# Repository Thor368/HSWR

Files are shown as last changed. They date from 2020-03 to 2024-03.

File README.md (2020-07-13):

# HSWR
Fork of the original VESC V6 to support up to 200V and 100A (depending on cooling)

#Work in progress (see http://vedder.se/forums/viewtopic.php?f=16&t=568)

#Gen1
Alpha Prototype on self etched boards. Never worked properly.

#Gen2
Four layer design in industry production quality. First working prototype.

#Gen3
Thicker copper layers for higher current capability. Had issues with current sampling.

#Gen3.1
Never was a board but a mod of Gen3. First prototype with Hall current sensors. Worked very well but needed a proper board.

#Gen4
- changed current sensors to halleffect sensors
- many changes in the IO (including connectors breaking backwards compatibility)
- HSWR can now interface with Tritium motor interface boards
- IO now fully isolated from HV
- fan drive
- changed MOSFET mounting mechanism for higher clamping force and reliablity
- some minimal mechanical changes breaking backwards compatibility to HSWR3 housing

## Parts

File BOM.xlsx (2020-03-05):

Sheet: Tabelle1
Reference(s) | Value | Footprint
C1, C12, C26, C29, C48, C49, C50, C51, C55, C56, C57, C58, C59 | 100n | Capacitor_SMD:C_0805_2012Metric
C2, C9 | 100u/16V | Capacitor_THT:CP_Radial_D6.3mm_P2.50mm
C3 | 22u/16V | Capacitor_SMD:C_0805_2012Metric
C4, C10, C11, C36 | 22u/6V3 | Capacitor_SMD:C_0805_2012Metric
C5, C6 | 2u2 | Capacitor_SMD:C_0805_2012Metric
C7, C8, C52, C53, C54 | 100n | Capacitor_SMD:C_0805_2012Metric
C13, C27, C30, C34, C35, C37, C38, C39, C40, C41, C42, C43, C44, C45, C46, C47 | 1u | Capacitor_SMD:C_0805_2012Metric
C14, C15, C17, C18, C19 | 330u 250V | Capacitor_THT:CP_Radial_D22.0mm_P10.00mm_SnapIn
C16, C28, C31 | 4n7 | Capacitor_SMD:C_0805_2012Metric
C20, C21, C22, C23, C24, C25 | 2u2 250V | Capacitor_SMD:C_2220_5650Metric
C32, C33 | 15p | Capacitor_SMD:C_0805_2012Metric
D1, D2, D3 | LED | LED_SMD:LED_0805_2012Metric
D10, D11, D12 | RFN2L4S | Diode_SMD:D_SOD-123
IC1 | B1212S-2W | Converter_DCDC:Converter_DCDC_muRata_NMAxxxxSC_THT
IC2, IC3 | JW5052C | Package_TO_SOT_SMD:TSOT-23-6
IC4 | ADUM3054 | Package_SO:SOIC-16W_7.5x10.3mm_P1.27mm
IC5 | ADuM4160 | Package_SO:SOIC-16W_7.5x10.3mm_P1.27mm
J1 | USB_B | Connector_USB:USB_B_TE_5787834_Vertical
J2 | IO | Connector_IDC:IDC-Header_2x08_P2.54mm_Vertical_Lock
J3 | B+ | MountingHole:MountingHole_6.5mm_Pad_Via
J4 | B- | MountingHole:MountingHole_6.5mm_Pad_Via
J5 | U | MountingHole:MountingHole_6.5mm_Pad_Via
J6 | V | MountingHole:MountingHole_6.5mm_Pad_Via
J7 | W | MountingHole:MountingHole_6.5mm_Pad_Via
J8 | SWD | Connector_PinHeader_2.54mm:PinHeader_2x03_P2.54mm_Vertical
J9 | AVR-ISP-6 | Connector_PinSocket_2.54mm:PinSocket_2x03_P2.54mm_Vertical
JP1 | H1 | Jumper:SolderJumper-2_P1.3mm_Open_TrianglePad1.0x1.5mm
JP2 | UART | Jumper:SolderJumper-3_P2.0mm_Open_TrianglePad1.0x1.5mm
JP3 | H2 | Jumper:SolderJumper-2_P1.3mm_Open_TrianglePad1.0x1.5mm
JP4 | H3 | Jumper:SolderJumper-2_P1.3mm_Open_TrianglePad1.0x1.5mm
L1, L2 | FCI201209F-4R7K | Inductor_SMD:L_0805_2012Metric
L3 | 22uH | Inductor_SMD:L_0805_2012Metric
NT1 | Net-Tie_2 | NetTie:NetTie-2_SMD_Pad2.0mm
Q1, Q2, Q3, Q4, Q5, Q6 | IXFK300N20X3 | Package_TO_SOT_THT:TO-264-3_Horizontal_TabUp
Q7 | Q_NMOS_GSD | Package_TO_SOT_SMD:SOT-23
R1, R37 | 100R | Resistor_SMD:R_0805_2012Metric
R2, R20, R23, R26, R36 | 1k | Resistor_SMD:R_0805_2012Metric
R3, R4, R33, R34, R40 | 120R | Resistor_SMD:R_0805_2012Metric
R5 | 470R | Resistor_SMD:R_0805_2012Metric
R6, R7 | 120R | Resistor_SMD:R_0805_2012Metric
R8, R27, R29, R31 | 300k 0.1% | Resistor_SMD:R_0805_2012Metric
R9, R28, R30, R32 | 4k7 0.1% | Resistor_SMD:R_0805_2012Metric
R10 | NTC | Resistor_SMD:R_0603_1608Metric
R11, R35 | 10k | Resistor_SMD:R_0805_2012Metric
R12, R13 | 100k | Resistor_SMD:R_0805_2012Metric
R14 | 110k | Resistor_SMD:R_0805_2012Metric
R15 | 15k | Resistor_SMD:R_0805_2012Metric
R16 | 49k9 | Resistor_SMD:R_0805_2012Metric
R17 | 11k | Resistor_SMD:R_0805_2012Metric
R18, R19, R21, R22, R24, R25 | 1R | Resistor_SMD:R_0805_2012Metric
R41, R42, R45, R46 | 22R | Resistor_SMD:R_0805_2012Metric
R43, R44 | 0R | Resistor_SMD:R_0805_2012Metric
U1, U2, U3 | ACS781xLRTR-150B | Sensor_Current:Allegro_PSOF-7_4.8x6.4mm_P1.60mm
U4 | STM32F405RGTx | Package_QFP:LQFP-64_10x10mm_P0.5mm
U5, U6, U7 | IRS2186 | Package_SO:SO-8_3.9x4.9mm_P1.27mm
U8 | AP1117-50 | Package_TO_SOT_SMD:SOT-223-3_TabPin2
U9 | ATtiny13A-SU | Package_SO:SOIJ-8_5.3x5.3mm_P1.27mm
U10 | AM26LV32xD | Package_SO:SOIC-16_3.9x9.9mm_P1.27mm
U11, U12 | ADuM120N | Package_SO:SOIC-8_3.9x4.9mm_P1.27mm
U13 | PC355 | Package_SO:SO-4_4.4x4.3mm_P2.54mm
Y1 | 8MHz | Crystal:Crystal_HC49-U_Vertical

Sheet: HSWR
Source:,"C:\Users\alexander.schroeder\git\HSWR\HSWR.sch"
Date:,"05.03.2020 09:08:09"
Tool:,"Eeschema (5.1.5)-3"
Generator:,"C:\Program Files\KiCad\bin\scripting\plugins/bom_csv_grouped_by_value.py"
Component Count:,"152"
Individual Components:
Item,"Qty","Reference(s)","Value","LibPart","Footprint","Datasheet"
,"","C1","100n","Device:C","Capacitor_SMD:C_0805_2012Metric",""
,"","C2","100u/16V","Device:CP_Small","Capacitor_THT:CP_Radial_D6.3mm_P2.50mm","~"
,"","C3","22u/16V","Device:C","Capacitor_SMD:C_0805_2012Metric","~"
,"","C4","22u/6V3","Device:C","Capacitor_SMD:C_0805_2012Metric","~"
,"","C5","2u2","Device:C_Small","Capacitor_SMD:C_0805_2012Metric","~"
,"","C6","2u2","Device:C_Small","Capacitor_SMD:C_0805_2012Metric","~"
,"","C7","100n","Device:C_Small","Capacitor_SMD:C_0805_2012Metric","~"
,"","C8","100n","Device:C_Small","Capacitor_SMD:C_0805_2012Metric","~"
,"","C9","100u/16V","Device:CP_Small","Capacitor_THT:CP_Radial_D6.3mm_P2.50mm","~"
,"","C10","22u/6V3","Device:C","Capacitor_SMD:C_0805_2012Metric","~"
,"","C11","22u/6V3","Device:C","Capacitor_SMD:C_0805_2012Metric","~"
,"","C12","100n","Device:C","Capacitor_SMD:C_0805_2012Metric","~"
,"","C13","1u","Device:C","Capacitor_SMD:C_0805_2012Metric","~"
,"","C14","330u 250V","Device:CP","Capacitor_THT:CP_Radial_D22.0mm_P10.00mm_SnapIn",""
,"","C15","330u 250V","Device:CP","Capacitor_THT:CP_Radial_D22.0mm_P10.00mm_SnapIn",""
,"","C16","4n7","Device:C","Capacitor_SMD:C_0805_2012Metric","~"
,"","C17","330u 250V","Device:CP","Capacitor_THT:CP_Radial_D22.0mm_P10.00mm_SnapIn",""
,"","C18","330u 250V","Device:CP","Capacitor_THT:CP_Radial_D22.0mm_P10.00mm_SnapIn",""
,"","C19","330u 250V","Device:CP","Capacitor_THT:CP_Radial_D22.0mm_P10.00mm_SnapIn",""
,"","C20","2u2 250V","Device:C","Capacitor_SMD:C_2220_5650Metric",""
,"","C21","2u2 250V","Device:C","Capacitor_SMD:C_2220_5650Metric",""
,"","C22","2u2 250V","Device:C","Capacitor_SMD:C_2220_5650Metric",""
,"","C23","2u2 250V","Device:C","Capacitor_SMD:C_2220_5650Metric",""
,"","C24","2u2 250V","Device:C","Capacitor_SMD:C_2220_5650Metric",""
,"","C25","2u2 250V","Device:C","Capacitor_SMD:C_2220_5650Metric",""
,"","C26","100n","Device:C","Capacitor_SMD:C_0805_2012Metric","~"
,"","C27","1u","Device:C","Capacitor_SMD:C_0805_2012Metric","~"
,"","C28","4n7","Device:C","Capacitor_SMD:C_0805_2012Metric","~"
,"","C29","100n","Device:C","Capacitor_SMD:C_0805_2012Metric","~"
,"","C30","1u","Device:C","Capacitor_SMD:C_0805_2012Metric","~"
,"","C31","4n7","Device:C","Capacitor_SMD:C_0805_2012Metric","~"
,"","C32","15p","Device:C","Capacitor_SMD:C_0805_2012Metric","~"
,"","C33","15p","Device:C","Capacitor_SMD:C_0805_2012Metric","~"
,"","C34","1u","Device:C","Capacitor_SMD:C_0805_2012Metric","~"
,"","C35","1u","Device:C","Capacitor_SMD:C_0805_2012Metric","~"
,"","C36","22u/6V3","Device:C","Capacitor_SMD:C_0805_2012Metric","~"
,"","C37","1u","Device:C","Capacitor_SMD:C_0805_2012Metric","~"
,"","C38","1u","Device:C","Capacitor_SMD:C_0805_2012Metric","~"
,"","C39","1u","Device:C","Capacitor_SMD:C_0805_2012Metric","~"
,"","C40","1u","Device:C","Capacitor_SMD:C_0805_2012Metric","~"
,"","C41","1u","Device:C","Capacitor_SMD:C_0805_2012Metric","~"
,"","C42","1u","Device:C","Capacitor_SMD:C_0805_2012Metric","~"
,"","C43","1u","Device:C","Capacitor_SMD:C_0805_2012Metric","~"
,"","C44","1u","Device:C","Capacitor_SMD:C_0805_2012Metric","~"
,"","C45","1u","Device:C","Capacitor_SMD:C_0805_2012Metric","~"
,"","C46","1u","Device:C","Capacitor_SMD:C_0805_2012Metric","~"
,"","C47","1u","Device:C","Capacitor_SMD:C_0805_2012Metric","~"
,"","C48","100n","Device:C","Capacitor_SMD:C_0805_2012Metric","~"
,"","C49","100n","Device:C","Capacitor_SMD:C_0805_2012Metric","~"
,"","C50","100n","Device:C","Capacitor_SMD:C_0805_2012Metric","~"
,"","C51","100n","Device:C","Capacitor_SMD:C_0805_2012Metric","~"
,"","C52","100n","Device:C_Small","Capacitor_SMD:C_0805_2012Metric",""
,"","C53","100n","Device:C_Small","Capacitor_SMD:C_0805_2012Metric",""
,"","C54","100n","Device:C_Small","Capacitor_SMD:C_0805_2012Metric",""
,"","C55","100n","Device:C","Capacitor_SMD:C_0805_2012Metric","~"
,"","C56","100n","Device:C","Capacitor_SMD:C_0805_2012Metric","~"
,"","C57","100n","Device:C","Capacitor_SMD:C_0805_2012Metric","~"
,"","C58","100n","Device:C","Capacitor_SMD:C_0805_2012Metric","~"
,"","C59","100n","Device:C","Capacitor_SMD:C_0805_2012Metric","~"
,"","D1","LED","Device:LED","LED_SMD:LED_0805_2012Metric","~"
,"","D2","LED","Device:LED","LED_SMD:LED_0805_2012Metric","~"
,"","D3","LED","Device:LED","LED_SMD:LED_0805_2012Metric","~"
,"","D10","RFN2L4S","Device:D_Small","Diode_SMD:D_SOD-123",""
,"","D11","RFN2L4S","Device:D_Small","Diode_SMD:D_SOD-123",""
,"","D12","RFN2L4S","Device:D_Small","Diode_SMD:D_SOD-123",""
,"","IC1","B1212S-2W","HSWR:DCDC_6pin","Converter_DCDC:Converter_DCDC_muRata_NMAxxxxSC_THT",""
,"","IC2","JW5052C","HSWR:JW5052C","Package_TO_SOT_SMD:TSOT-23-6",""
,"","IC3","JW5052C","HSWR:JW5052C","Package_TO_SOT_SMD:TSOT-23-6",""
,"","IC4","ADUM3054","HSWR:ADUM3054","Package_SO:SOIC-16W_7.5x10.3mm_P1.27mm",""
,"","IC5","ADuM4160","Interface_USB:ADUM4160","Package_SO:SOIC-16W_7.5x10.3mm_P1.27mm",""
,"","J1","USB_B","Connector:USB_B","Connector_USB:USB_B_TE_5787834_Vertical"," ~"
,"","J2","IO","Connector:Conn_01x16_Male","Connector_IDC:IDC-Header_2x08_P2.54mm_Vertical_Lock","~"
,"","J3","B+","Connector:Conn_01x01_Male","MountingHole:MountingHole_6.5mm_Pad_Via","~"
,"","J4","B-","Connector:Conn_01x01_Male","MountingHole:MountingHole_6.5mm_Pad_Via","~"
,"","J5","U","Connector:Conn_01x01_Male","MountingHole:MountingHole_6.5mm_Pad_Via","~"
,"","J6","V","Connector:Conn_01x01_Male","MountingHole:MountingHole_6.5mm_Pad_Via","~"
,"","J7","W","Connector:Conn_01x01_Male","MountingHole:MountingHole_6.5mm_Pad_Via","~"
,"","J8","SWD","Connector:Conn_01x06_Male","Connector_PinHeader_2.54mm:PinHeader_2x03_P2.54mm_Vertical","~"
,"","J9","AVR-ISP-6","Connector:AVR-ISP-6","Connector_PinSocket_2.54mm:PinSocket_2x03_P2.54mm_Vertical"," ~"
,"","JP1","H1","Device:Jumper_NO_Small","Jumper:SolderJumper-2_P1.3mm_Open_TrianglePad1.0x1.5mm","~"
,"","JP2","UART","Jumper:SolderJumper_3_Open","Jumper:SolderJumper-3_P2.0mm_Open_TrianglePad1.0x1.5mm","~"
,"","JP3","H2","Device:Jumper_NO_Small","Jumper:SolderJumper-2_P1.3mm_Open_TrianglePad1.0x1.5mm","~"
,"","JP4","H3","Device:Jumper_NO_Small","Jumper:SolderJumper-2_P1.3mm_Open_TrianglePad1.0x1.5mm","~"
,"","L1","FCI201209F-4R7K","Device:L","Inductor_SMD:L_0805_2012Metric","~"
,"","L2","FCI201209F-4R7K","Device:L","Inductor_SMD:L_0805_2012Metric","~"
,"","L3","22uH","Device:L","Inductor_SMD:L_0805_2012Metric","~"
,"","NT1","Net-Tie_2","Device:Net-Tie_2","NetTie:NetTie-2_SMD_Pad2.0mm","~"
,"","Q1","IXFK300N20X3","Device:Q_NMOS_GDS","Package_TO_SOT_THT:TO-264-3_Horizontal_TabUp",""
,"","Q2","IXFK300N20X3","Device:Q_NMOS_GDS","Package_TO_SOT_THT:TO-264-3_Horizontal_TabUp",""
,"","Q3","IXFK300N20X3","Device:Q_NMOS_GDS","Package_TO_SOT_THT:TO-264-3_Horizontal_TabUp",""
,"","Q4","IXFK300N20X3","Device:Q_NMOS_GDS","Package_TO_SOT_THT:TO-264-3_Horizontal_TabUp",""
,"","Q5","IXFK300N20X3","Device:Q_NMOS_GDS","Package_TO_SOT_THT:TO-264-3_Horizontal_TabUp",""
,"","Q6","IXFK300N20X3","Device:Q_NMOS_GDS","Package_TO_SOT_THT:TO-264-3_Horizontal_TabUp",""
,"","Q7","Q_NMOS_GSD","Device:Q_NMOS_GSD","Package_TO_SOT_SMD:SOT-23","~"
,"","R1","100R","Device:R","Resistor_SMD:R_0805_2012Metric","~"
,"","R2","1k","Device:R","Resistor_SMD:R_0805_2012Metric","~"
,"","R3","120R","Device:R_Small","Resistor_SMD:R_0805_2012Metric","~"
,"","R4","120R","Device:R_Small","Resistor_SMD:R_0805_2012Metric","~"
,"","R5","470R","Device:R","Resistor_SMD:R_0805_2012Metric","~"
,"","R6","120R","Device:R","Resistor_SMD:R_0805_2012Metric","~"
,"","R7","120R","Device:R","Resistor_SMD:R_0805_2012Metric","~"
,"","R8","300k 0.1%","Device:R","Resistor_SMD:R_0805_2012Metric",""
,"","R9","4k7 0.1%","Device:R","Resistor_SMD:R_0805_2012Metric",""
,"","R10","NTC","Device:Thermistor_NTC","Resistor_SMD:R_0603_1608Metric","~"
,"","R11","10k","Device:R","Resistor_SMD:R_0805_2012Metric","~"
,"","R12","100k","Device:R_Small","Resistor_SMD:R_0805_2012Metric","~"
,"","R13","100k","Device:R_Small","Resistor_SMD:R_0805_2012Metric","~"
,"","R14","110k","Device:R_Small","Resistor_SMD:R_0805_2012Metric","~"
,"","R15","15k","Device:R_Small","Resistor_SMD:R_0805_2012Metric","~"
,"","R16","49k9","Device:R_Small","Resistor_SMD:R_0805_2012Metric","~"
,"","R17","11k","Device:R_Small","Resistor_SMD:R_0805_2012Metric","~"
,"","R18","1R","Device:R","Resistor_SMD:R_0805_2012Metric",""
,"","R19","1R","Device:R","Resistor_SMD:R_0805_2012Metric",""
,"","R20","1k","Device:R","Resistor_SMD:R_0805_2012Metric","~"
,"","R21","1R","Device:R","Resistor_SMD:R_0805_2012Metric",""
,"","R22","1R","Device:R","Resistor_SMD:R_0805_2012Metric",""
,"","R23","1k","Device:R","Resistor_SMD:R_0805_2012Metric","~"
,"","R24","1R","Device:R","Resistor_SMD:R_0805_2012Metric",""
,"","R25","1R","Device:R","Resistor_SMD:R_0805_2012Metric",""
,"","R26","1k","Device:R","Resistor_SMD:R_0805_2012Metric","~"
,"","R27","300k 0.1%","Device:R","Resistor_SMD:R_0805_2012Metric","~"
,"","R28","4k7 0.1%","Device:R","Resistor_SMD:R_0805_2012Metric","~"
,"","R29","300k 0.1%","Device:R","Resistor_SMD:R_0805_2012Metric","~"
,"","R30","4k7 0.1%","Device:R","Resistor_SMD:R_0805_2012Metric","~"
,"","R31","300k 0.1%","Device:R","Resistor_SMD:R_0805_2012Metric","~"
,"","R32","4k7 0.1%","Device:R","Resistor_SMD:R_0805_2012Metric","~"
,"","R33","120R","Device:R_Small","Resistor_SMD:R_0805_2012Metric","~"
,"","R34","120R","Device:R_Small","Resistor_SMD:R_0805_2012Metric","~"
,"","R35","10k","Device:R","Resistor_SMD:R_0805_2012Metric","~"
,"","R36","1k","Device:R","Resistor_SMD:R_0805_2012Metric","~"
,"","R37","100R","Device:R","Resistor_SMD:R_0805_2012Metric","~"
,"","R40","120R","Device:R_Small","Resistor_SMD:R_0805_2012Metric",""
,"","R41","22R","Device:R","Resistor_SMD:R_0805_2012Metric","~"
,"","R42","22R","Device:R","Resistor_SMD:R_0805_2012Metric","~"
,"","R43","0R","Device:R","Resistor_SMD:R_0805_2012Metric","~"
,"","R44","0R","Device:R","Resistor_SMD:R_0805_2012Metric","~"
,"","R45","22R","Device:R","Resistor_SMD:R_0805_2012Metric","~"
,"","R46","22R","Device:R","Resistor_SMD:R_0805_2012Metric","~"
,"","U1","ACS781xLRTR-150B","Sensor_Current:ACS781xLRTR-150B","Sensor_Current:Allegro_PSOF-7_4.8x6.4mm_P1.60mm","http://www.allegromicro.com/~/media/Files/Datasheets/ACS781-Datsaheet.ashx?la=en"
,"","U2","ACS781xLRTR-150B","Sensor_Current:ACS781xLRTR-150B","Sensor_Current:Allegro_PSOF-7_4.8x6.4mm_P1.60mm","http://www.allegromicro.com/~/media/Files/Datasheets/ACS781-Datsaheet.ashx?la=en"
,"","U3","ACS781xLRTR-150B","Sensor_Current:ACS781xLRTR-150B","Sensor_Current:Allegro_PSOF-7_4.8x6.4mm_P1.60mm","http://www.allegromicro.com/~/media/Files/Datasheets/ACS781-Datsaheet.ashx?la=en"
,"","U4","STM32F405RGTx","MCU_ST_STM32F4:STM32F405RGTx","Package_QFP:LQFP-64_10x10mm_P0.5mm","http://www.st.com/st-web-ui/static/active/en/resource/technical/document/datasheet/DM00037051.pdf"
,"","U5","IRS2186","Driver_FET:IRS2186","Package_SO:SO-8_3.9x4.9mm_P1.27mm","http://www.irf.com/product-info/datasheets/data/irs2186pbf.pdf"
,"","U6","IRS2186","Driver_FET:IRS2186","Package_SO:SO-8_3.9x4.9mm_P1.27mm","http://www.irf.com/product-info/datasheets/data/irs2186pbf.pdf"
,"","U7","IRS2186","Driver_FET:IRS2186","Package_SO:SO-8_3.9x4.9mm_P1.27mm","http://www.irf.com/product-info/datasheets/data/irs2186pbf.pdf"
,"","U8","AP1117-50","HSWR:AP1117-50","Package_TO_SOT_SMD:SOT-223-3_TabPin2","http://www.diodes.com/datasheets/AP1117.pdf"
,"","U9","ATtiny13A-SU","MCU_Microchip_ATtiny:ATtiny13A-SU","Package_SO:SOIJ-8_5.3x5.3mm_P1.27mm","http://ww1.microchip.com/downloads/en/DeviceDoc/doc8126.pdf"
,"","U10","AM26LV32xD","Interface:AM26LV32xD","Package_SO:SOIC-16_3.9x9.9mm_P1.27mm","http://www.ti.com/lit/ds/symlink/am26lv32.pdf"
,"","U11","ADuM120N","Isolator:ADuM120N","Package_SO:SOIC-8_3.9x4.9mm_P1.27mm","https://www.analog.com/media/en/technical-documentation/data-sheets/ADuM120N_121N.pdf"
,"","U12","ADuM120N","Isolator:ADuM120N","Package_SO:SOIC-8_3.9x4.9mm_P1.27mm","https://www.analog.com/media/en/technical-documentation/data-sheets/ADuM120N_121N.pdf"
,"","U13","PC355","Isolator:SFH617A-1","Package_SO:SO-4_4.4x4.3mm_P2.54mm","http://www.vishay.com/docs/83740/sfh617a.pdf"
,"","Y1","8MHz","Device:Crystal","Crystal:Crystal_HC49-U_Vertical","~"
Collated Components:
Item,"Qty","Reference(s)","Value","LibPart","Footprint","Datasheet"
1,"13","C1, C12, C26, C29, C48, C49, C50, C51, C55, C56, C57, C58, C59","100n","Device:C","Capacitor_SMD:C_0805_2012Metric","~"
2,"2","C2, C9","100u/16V","Device:CP_Small","Capacitor_THT:CP_Radial_D6.3mm_P2.50mm","~"
3,"1","C3","22u/16V","Device:C","Capacitor_SMD:C_0805_2012Metric","~"
4,"4","C4, C10, C11, C36","22u/6V3","Device:C","Capacitor_SMD:C_0805_2012Metric","~"
5,"2","C5, C6","2u2","Device:C_Small","Capacitor_SMD:C_0805_2012Metric","~"
6,"5","C7, C8, C52, C53, C54","100n","Device:C_Small","Capacitor_SMD:C_0805_2012Metric","~"
7,"16","C13, C27, C30, C34, C35, C37, C38, C39, C40, C41, C42, C43, C44, C45, C46, C47","1u","Device:C","Capacitor_SMD:C_0805_2012Metric","~"
8,"5","C14, C15, C17, C18, C19","330u 250V","Device:CP","Capacitor_THT:CP_Radial_D22.0mm_P10.00mm_SnapIn",""
9,"3","C16, C28, C31","4n7","Device:C","Capacitor_SMD:C_0805_2012Metric","~"
10,"6","C20, C21, C22, C23, C24, C25","2u2 250V","Device:C","Capacitor_SMD:C_2220_5650Metric",""
11,"2","C32, C33","15p","Device:C","Capacitor_SMD:C_0805_2012Metric","~"
12,"3","D1, D2, D3","LED","Device:LED","LED_SMD:LED_0805_2012Metric","~"
13,"3","D10, D11, D12","RFN2L4S","Device:D_Small","Diode_SMD:D_SOD-123",""
14,"1","IC1","B1212S-2W","HSWR:DCDC_6pin","Converter_DCDC:Converter_DCDC_muRata_NMAxxxxSC_THT",""
15,"2","IC2, IC3","JW5052C","HSWR:JW5052C","Package_TO_SOT_SMD:TSOT-23-6",""
16,"1","IC4","ADUM3054","HSWR:ADUM3054","Package_SO:SOIC-16W_7.5x10.3mm_P1.27mm",""
17,"1","IC5","ADuM4160","Interface_USB:ADUM4160","Package_SO:SOIC-16W_7.5x10.3mm_P1.27mm",""
18,"1","J1","USB_B","Connector:USB_B","Connector_USB:USB_B_TE_5787834_Vertical"," ~"
19,"1","J2","IO","Connector:Conn_01x16_Male","Connector_IDC:IDC-Header_2x08_P2.54mm_Vertical_Lock","~"
20,"1","J3","B+","Connector:Conn_01x01_Male","MountingHole:MountingHole_6.5mm_Pad_Via","~"
21,"1","J4","B-","Connector:Conn_01x01_Male","MountingHole:MountingHole_6.5mm_Pad_Via","~"
22,"1","J5","U","Connector:Conn_01x01_Male","MountingHole:MountingHole_6.5mm_Pad_Via","~"
23,"1","J6","V","Connector:Conn_01x01_Male","MountingHole:MountingHole_6.5mm_Pad_Via","~"
24,"1","J7","W","Connector:Conn_01x01_Male","MountingHole:MountingHole_6.5mm_Pad_Via","~"
25,"1","J8","SWD","Connector:Conn_01x06_Male","Connector_PinHeader_2.54mm:PinHeader_2x03_P2.54mm_Vertical","~"
26,"1","J9","AVR-ISP-6","Connector:AVR-ISP-6","Connector_PinSocket_2.54mm:PinSocket_2x03_P2.54mm_Vertical"," ~"
27,"1","JP1","H1","Device:Jumper_NO_Small","Jumper:SolderJumper-2_P1.3mm_Open_TrianglePad1.0x1.5mm","~"
28,"1","JP2","UART","Jumper:SolderJumper_3_Open","Jumper:SolderJumper-3_P2.0mm_Open_TrianglePad1.0x1.5mm","~"
29,"1","JP3","H2","Device:Jumper_NO_Small","Jumper:SolderJumper-2_P1.3mm_Open_TrianglePad1.0x1.5mm","~"
30,"1","JP4","H3","Device:Jumper_NO_Small","Jumper:SolderJumper-2_P1.3mm_Open_TrianglePad1.0x1.5mm","~"
31,"2","L1, L2","FCI201209F-4R7K","Device:L","Inductor_SMD:L_0805_2012Metric","~"
32,"1","L3","22uH","Device:L","Inductor_SMD:L_0805_2012Metric","~"
33,"1","NT1","Net-Tie_2","Device:Net-Tie_2","NetTie:NetTie-2_SMD_Pad2.0mm","~"
34,"6","Q1, Q2, Q3, Q4, Q5, Q6","IXFK300N20X3","Device:Q_NMOS_GDS","Package_TO_SOT_THT:TO-264-3_Horizontal_TabUp",""
35,"1","Q7","Q_NMOS_GSD","Device:Q_NMOS_GSD","Package_TO_SOT_SMD:SOT-23","~"
36,"2","R1, R37","100R","Device:R","Resistor_SMD:R_0805_2012Metric","~"
37,"5","R2, R20, R23, R26, R36","1k","Device:R","Resistor_SMD:R_0805_2012Metric","~"
38,"5","R3, R4, R33, R34, R40","120R","Device:R_Small","Resistor_SMD:R_0805_2012Metric","~"
39,"1","R5","470R","Device:R","Resistor_SMD:R_0805_2012Metric","~"
40,"2","R6, R7","120R","Device:R","Resistor_SMD:R_0805_2012Metric","~"
41,"4","R8, R27, R29, R31","300k 0.1%","Device:R","Resistor_SMD:R_0805_2012Metric","~"
42,"4","R9, R28, R30, R32","4k7 0.1%","Device:R","Resistor_SMD:R_0805_2012Metric","~"
43,"1","R10","NTC","Device:Thermistor_NTC","Resistor_SMD:R_0603_1608Metric","~"
44,"2","R11, R35","10k","Device:R","Resistor_SMD:R_0805_2012Metric","~"
45,"2","R12, R13","100k","Device:R_Small","Resistor_SMD:R_0805_2012Metric","~"
46,"1","R14","110k","Device:R_Small","Resistor_SMD:R_0805_2012Metric","~"
47,"1","R15","15k","Device:R_Small","Resistor_SMD:R_0805_2012Metric","~"
48,"1","R16","49k9","Device:R_Small","Resistor_SMD:R_0805_2012Metric","~"
49,"1","R17","11k","Device:R_Small","Resistor_SMD:R_0805_2012Metric","~"
50,"6","R18, R19, R21, R22, R24, R25","1R","Device:R","Resistor_SMD:R_0805_2012Metric",""
51,"4","R41, R42, R45, R46","22R","Device:R","Resistor_SMD:R_0805_2012Metric","~"
52,"2","R43, R44","0R","Device:R","Resistor_SMD:R_0805_2012Metric","~"
53,"3","U1, U2, U3","ACS781xLRTR-150B","Sensor_Current:ACS781xLRTR-150B","Sensor_Current:Allegro_PSOF-7_4.8x6.4mm_P1.60mm","http://www.allegromicro.com/~/media/Files/Datasheets/ACS781-Datsaheet.ashx?la=en"
54,"1","U4","STM32F405RGTx","MCU_ST_STM32F4:STM32F405RGTx","Package_QFP:LQFP-64_10x10mm_P0.5mm","http://www.st.com/st-web-ui/static/active/en/resource/technical/document/datasheet/DM00037051.pdf"
55,"3","U5, U6, U7","IRS2186","Driver_FET:IRS2186","Package_SO:SO-8_3.9x4.9mm_P1.27mm","http://www.irf.com/product-info/datasheets/data/irs2186pbf.pdf"
56,"1","U8","AP1117-50","HSWR:AP1117-50","Package_TO_SOT_SMD:SOT-223-3_TabPin2","http://www.diodes.com/datasheets/AP1117.pdf"
57,"1","U9","ATtiny13A-SU","MCU_Microchip_ATtiny:ATtiny13A-SU","Package_SO:SOIJ-8_5.3x5.3mm_P1.27mm","http://ww1.microchip.com/downloads/en/DeviceDoc/doc8126.pdf"
58,"1","U10","AM26LV32xD","Interface:AM26LV32xD","Package_SO:SOIC-16_3.9x9.9mm_P1.27mm","http://www.ti.com/lit/ds/symlink/am26lv32.pdf"
59,"2","U11, U12","ADuM120N","Isolator:ADuM120N","Package_SO:SOIC-8_3.9x4.9mm_P1.27mm","https://www.analog.com/media/en/technical-documentation/data-sheets/ADuM120N_121N.pdf"
60,"1","U13","PC355","Isolator:SFH617A-1","Package_SO:SO-4_4.4x4.3mm_P2.54mm","http://www.vishay.com/docs/83740/sfh617a.pdf"
61,"1","Y1","8MHz","Device:Crystal","Crystal:Crystal_HC49-U_Vertical","~"

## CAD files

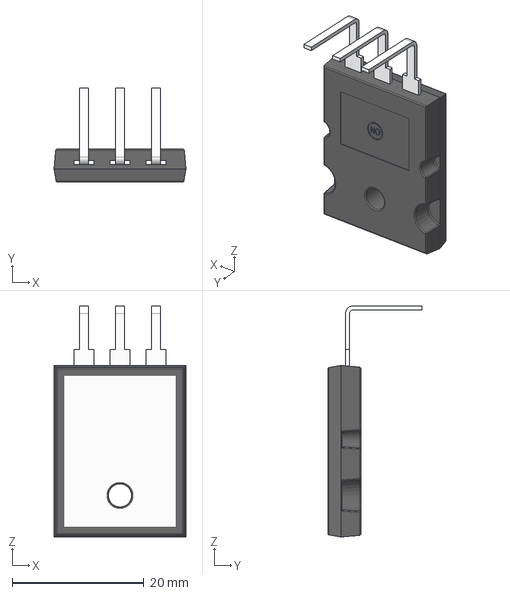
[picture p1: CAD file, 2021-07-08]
TO-264-3-HM.step
20.0 x 14.3 x 35.0 mm

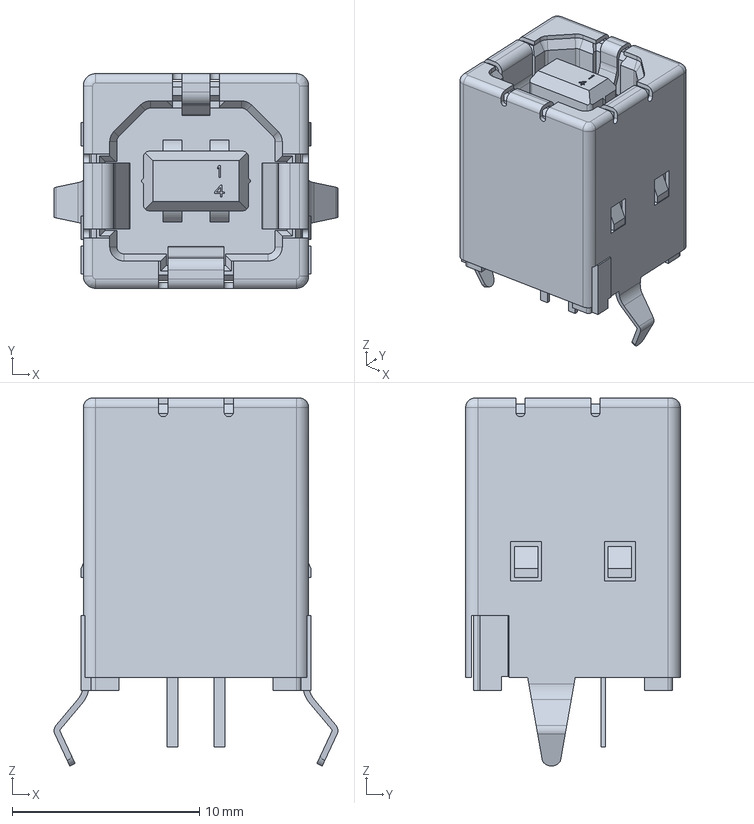
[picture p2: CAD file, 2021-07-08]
USB B vert.step
15.1 x 11.5 x 19.6 mm

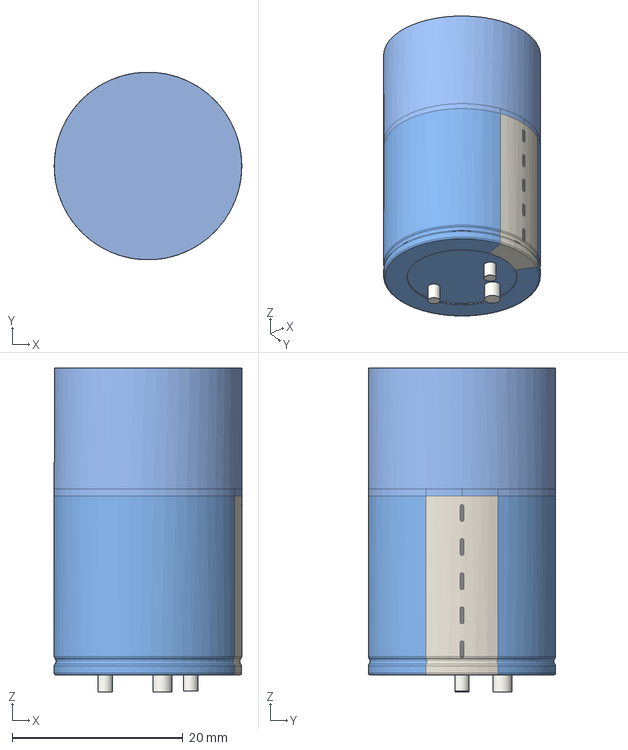
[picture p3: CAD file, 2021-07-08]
CP_Radial_D220mm_P1000mm_3pin_SnapIn.step
22.0 x 22.0 x 38.0 mm

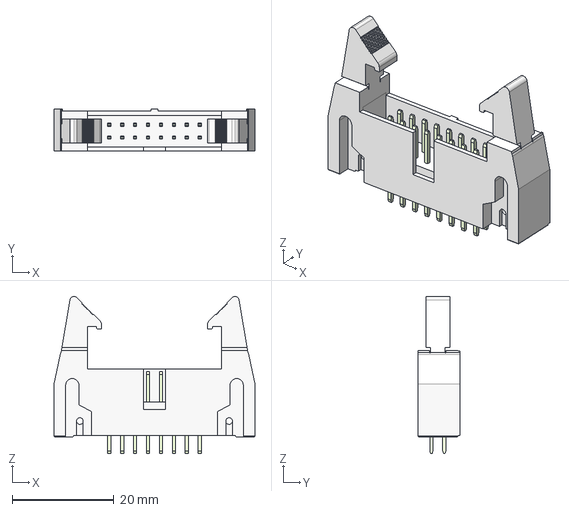
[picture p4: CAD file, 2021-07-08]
header_awh16g-0232-t.step
39.5 x 8.30 x 30.9 mm

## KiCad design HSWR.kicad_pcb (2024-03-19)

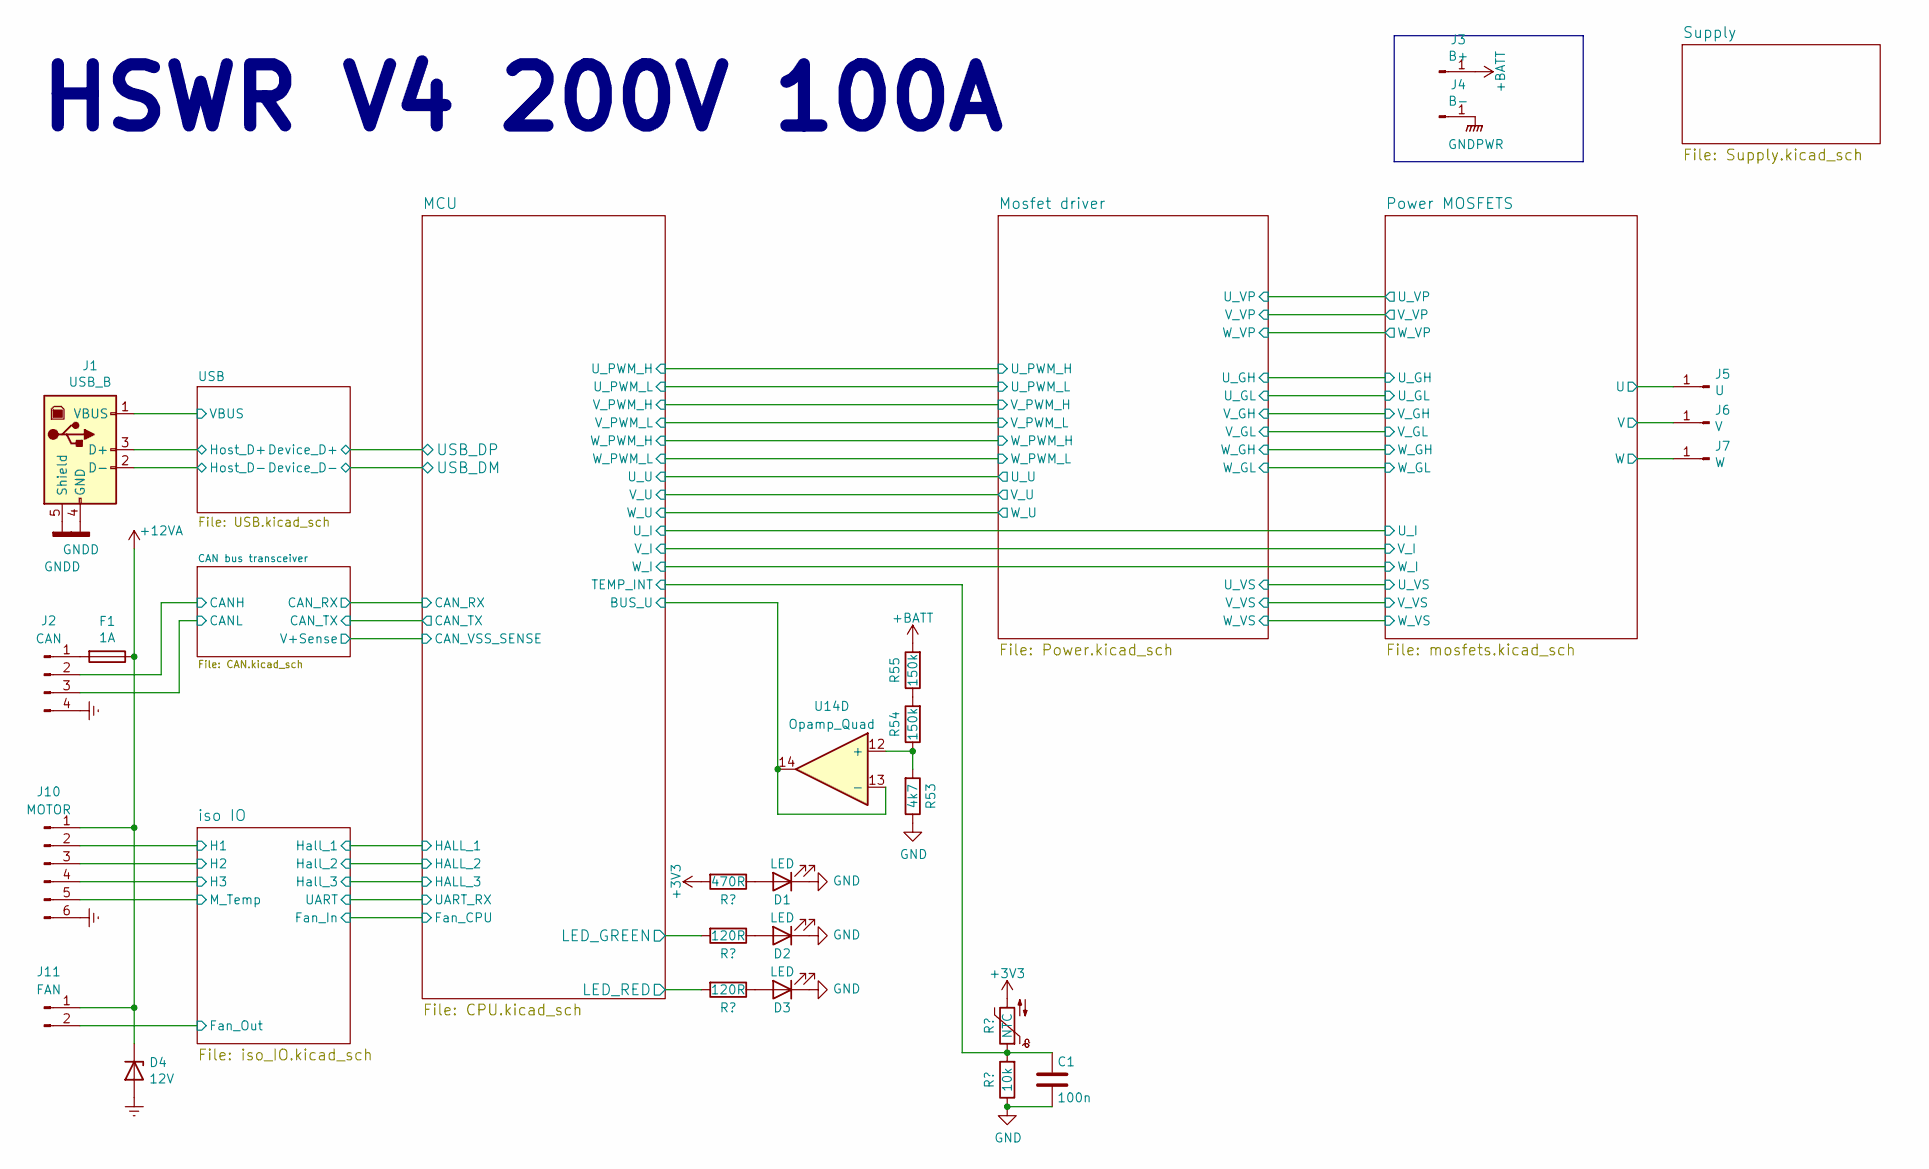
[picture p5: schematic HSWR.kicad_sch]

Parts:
C1: 100n; C_0805_2012Metric
D1, D2, D3: LED; LED_0805_2012Metric
D4: 12V; D_SMA
F1: 1A; Fuse_Littelfuse-NANO2-451_453
J1: USB_B; USB_B_TE_5787834_Vertical
J2: CAN; PhoenixContact_MCV_1,5_4-G-3.5_1x04_P3.50mm_Vertical
J3: B+; MountingHole_6.5mm_Pad_Via
J4: B-; MountingHole_6.5mm_Pad_Via
J5: U; MountingHole_6.5mm_Pad_Via
J6: V; MountingHole_6.5mm_Pad_Via
J7: W; MountingHole_6.5mm_Pad_Via
J10: MOTOR; PhoenixContact_MCV_1,5_6-G-3.5_1x06_P3.50mm_Vertical
J11: FAN; PhoenixContact_MCV_1,5_2-G-3.5_1x02_P3.50mm_Vertical
R5: 470R; R_0805_2012Metric
R6, R7: 120R; R_0805_2012Metric
R10: NTC; R_0603_1608Metric
R11: 10k; R_0805_2012Metric
R53: 4k7; R_0805_2012Metric
R54, R55: 150k; R_0805_2012Metric
U14: Opamp_Quad; SO-14_3.9x8.65mm_P1.27mm

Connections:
+3V3: R5.2, R10.2; also elsewhere on the board
+12VA: D4.1 (K), F1.1, J10.1, J11.1; also elsewhere on the board
+BATT: J3.1, R55.2; also elsewhere on the board
/CAN bus transceiver/CANH: J2.2; also elsewhere on the board
/CAN bus transceiver/CANL: J2.3; also elsewhere on the board
/MCU/BUS_U: U14.13 (-), U14.14; also elsewhere on the board
/MCU/LED_GREEN: R6.2; also elsewhere on the board
/MCU/LED_RED: R7.2; also elsewhere on the board
/MCU/TEMP_INT: C1.1, R10.1, R11.2; also elsewhere on the board
/Power MOSFETS/U: J5.1; also elsewhere on the board
/Power MOSFETS/V: J6.1; also elsewhere on the board
/Power MOSFETS/W: J7.1; also elsewhere on the board
/USB/Host_D+: J1.3 (D+); also elsewhere on the board
/USB/Host_D-: J1.2 (D-); also elsewhere on the board
/USB/VBUS: J1.1 (VBUS); also elsewhere on the board
/iso IO/Fan_Out: J11.2; also elsewhere on the board
/iso IO/H1: J10.2; also elsewhere on the board
/iso IO/H2: J10.3; also elsewhere on the board
/iso IO/H3: J10.4; also elsewhere on the board
/iso IO/M_Temp: J10.5; also elsewhere on the board
Earth: D4.2 (A), J2.4, J10.6; also elsewhere on the board
GND: C1.2, D1.1 (K), D2.1 (K), D3.1 (K), R11.1, R53.1; also elsewhere on the board
GNDD: J1.4 (GND), J1.5 (Shield); also elsewhere on the board
GNDPWR: J4.1; also elsewhere on the board
unnamed: D1.2 (A), R5.1
unnamed: D2.2 (A), R6.1
unnamed: D3.2 (A), R7.1
unnamed: F1.2, J2.1
unnamed: R54.2, R55.1
unnamed: R53.2, R54.1, U14.12 (+)

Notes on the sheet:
HSWR V4 200V 100A

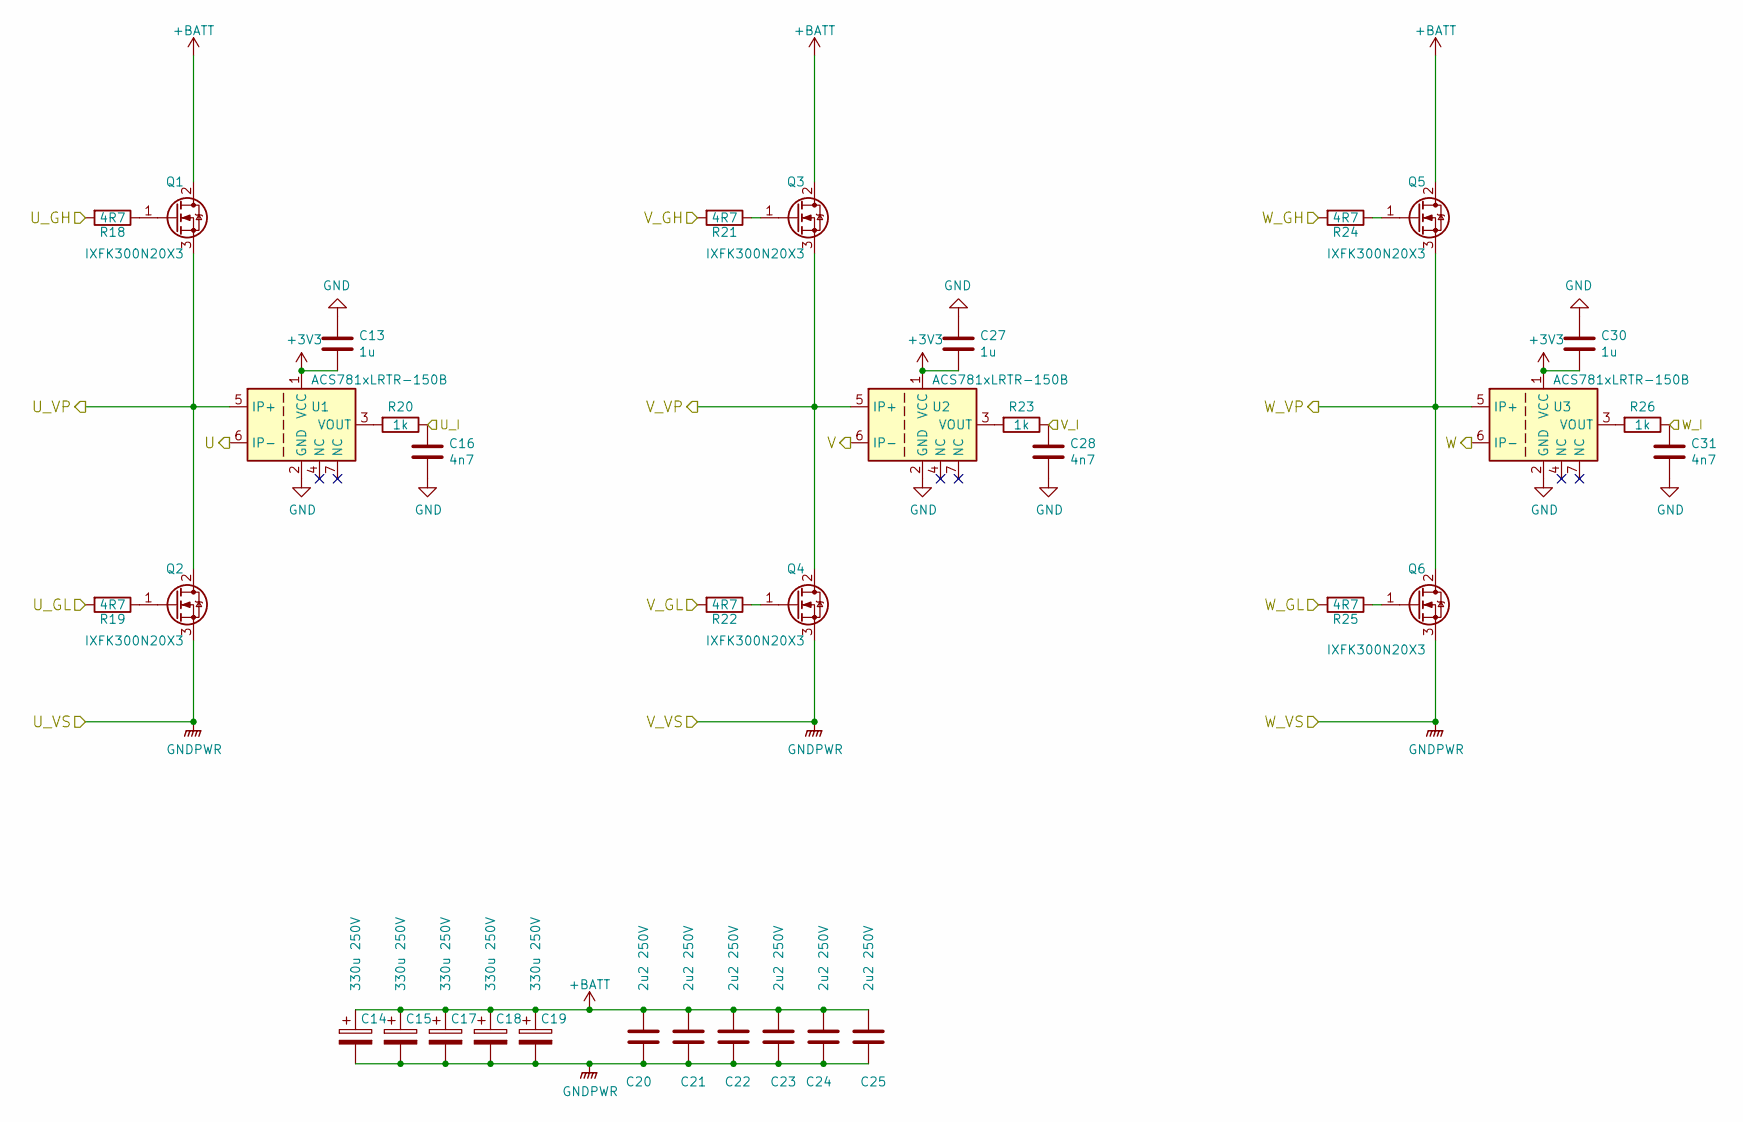
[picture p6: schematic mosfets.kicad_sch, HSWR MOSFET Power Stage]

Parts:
C13, C27, C30: 1u; C_0805_2012Metric
C14, C15, C17, C18, C19: 330u 250V; CP_Radial_D22.0mm_P10.00mm_SnapIn
C16, C28, C31: 4n7; C_0805_2012Metric
C20, C21, C22, C23, C24, C25: 2u2 250V; C_2220_5750Metric
Q1, Q2, Q3, Q4, Q5, Q6: IXFK300N20X3; TO-264-3_Horizontal_TabUp_6mm_hole
R18, R19, R21, R22, R24, R25: 4R7; R_0805_2012Metric
R20, R23, R26: 1k; R_0805_2012Metric
U1, U2, U3: ACS781xLRTR-150B; Allegro_PSOF-7_4.8x6.4mm_P1.60mm

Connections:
+3V3: C13.2, C27.2, C30.2, U1.1 (VCC), U2.1 (VCC), U3.1 (VCC); also elsewhere on the board
+BATT: C14.1, C15.1, C17.1, C18.1, C19.1, C20.1, C21.1, C22.1, C23.1, C24.1, C25.1, Q1.2 (D), Q3.2 (D), Q5.2 (D); also elsewhere on the board
/MCU/U_I: C16.1, R20.1; also elsewhere on the board
/MCU/V_I: C28.1, R23.1; also elsewhere on the board
/MCU/W_I: C31.1, R26.1; also elsewhere on the board
/Mosfet driver/U_GH: R18.2; also elsewhere on the board
/Mosfet driver/U_GL: R19.2; also elsewhere on the board
/Mosfet driver/U_VP: Q1.3 (S), Q2.2 (D), U1.5 (IP+); also elsewhere on the board
/Mosfet driver/V_GH: R21.2; also elsewhere on the board
/Mosfet driver/V_GL: R22.2; also elsewhere on the board
/Mosfet driver/V_VP: Q3.3 (S), Q4.2 (D), U2.5 (IP+); also elsewhere on the board
/Mosfet driver/W_GH: R24.2; also elsewhere on the board
/Mosfet driver/W_GL: R25.2; also elsewhere on the board
/Mosfet driver/W_VP: Q5.3 (S), Q6.2 (D), U3.5 (IP+); also elsewhere on the board
/Power MOSFETS/U: U1.6 (IP-); also elsewhere on the board
/Power MOSFETS/V: U2.6 (IP-); also elsewhere on the board
/Power MOSFETS/W: U3.6 (IP-); also elsewhere on the board
GND: C13.1, C16.2, C27.1, C28.2, C30.1, C31.2, U1.2 (GND), U2.2 (GND), U3.2 (GND); also elsewhere on the board
GNDPWR: C14.2, C15.2, C17.2, C18.2, C19.2, C20.2, C21.2, C22.2, C23.2, C24.2, C25.2, Q2.3 (S), Q4.3 (S), Q6.3 (S); also elsewhere on the board
unnamed: Q1.1 (G), R18.1
unnamed: Q2.1 (G), R19.1
unnamed: Q3.1 (G), R21.1
unnamed: Q4.1 (G), R22.1
unnamed: Q5.1 (G), R24.1
unnamed: Q6.1 (G), R25.1
unnamed: R20.2, U1.3 (VOUT)
unnamed: R23.2, U2.3 (VOUT)
unnamed: R26.2, U3.3 (VOUT)

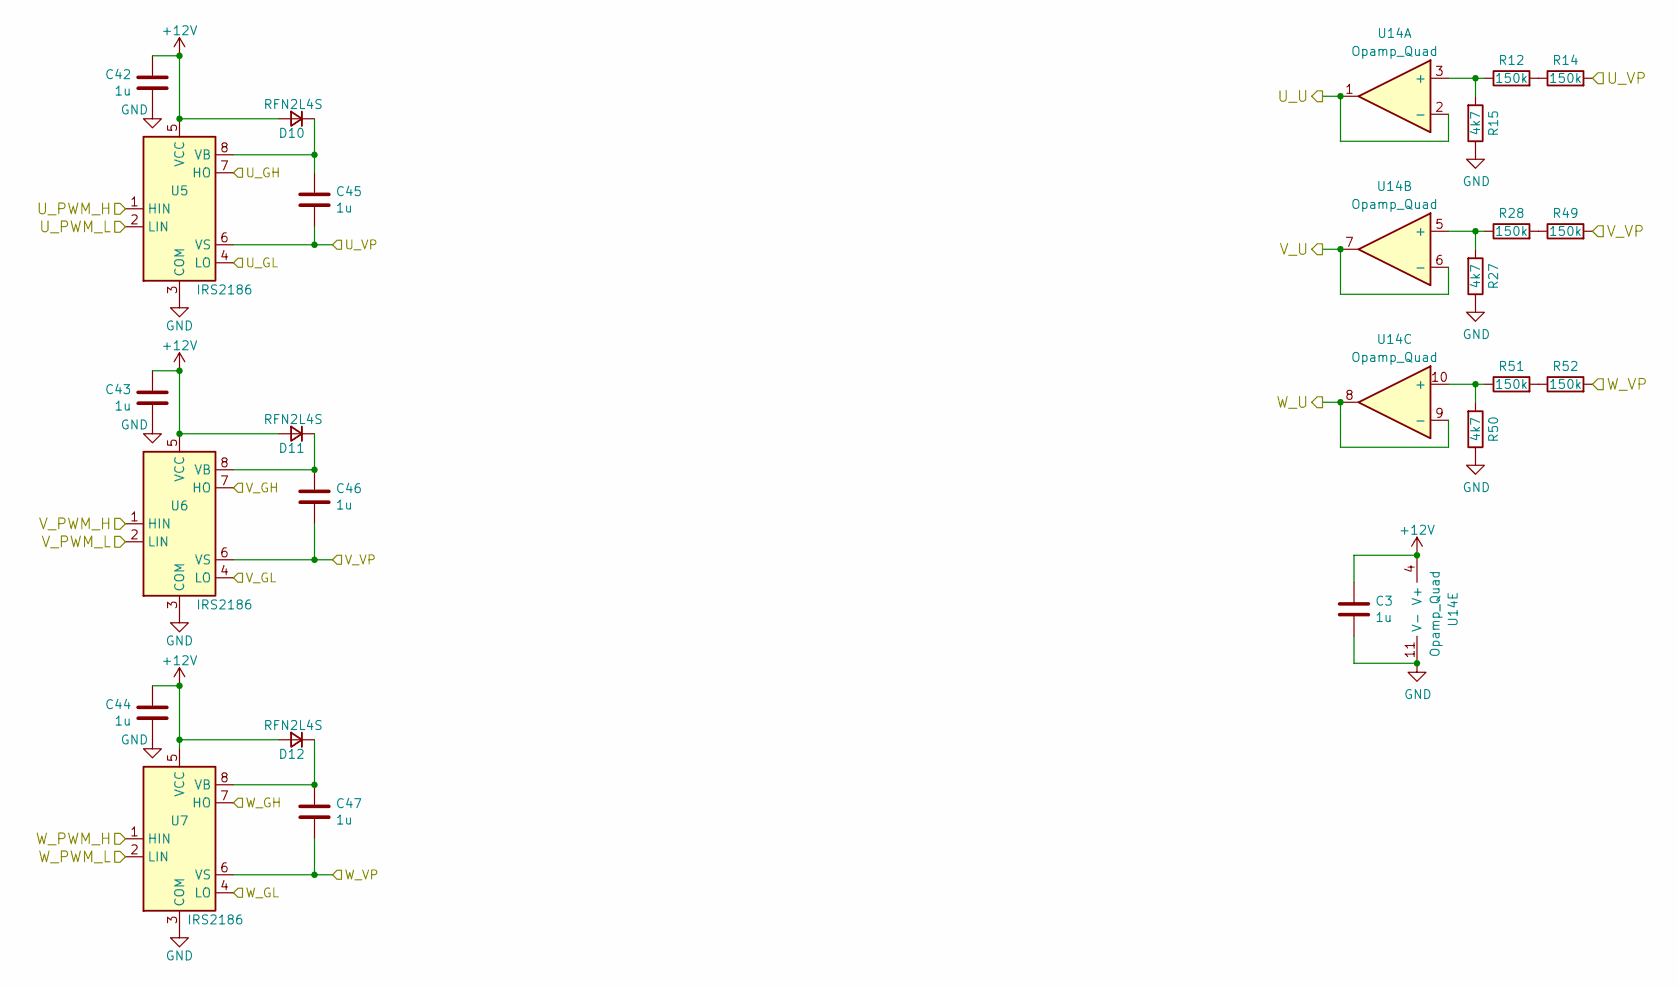
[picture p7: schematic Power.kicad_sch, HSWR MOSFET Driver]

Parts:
C3, C42, C43, C44, C45, C46, C47: 1u; C_0805_2012Metric
D10, D11, D12: RFN2L4S; D_SOD-123
R12, R14, R28, R49, R51, R52: 150k; R_0805_2012Metric
R15, R27, R50: 4k7; R_0805_2012Metric
U5, U6, U7: IRS2186; SOIC-8_3.9x4.9mm_P1.27mm
U14: Opamp_Quad; SO-14_3.9x8.65mm_P1.27mm

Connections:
+12V: C3.1, C42.2, C43.2, C44.2, D10.2 (A), D11.2 (A), D12.2 (A), U5.5 (VCC), U6.5 (VCC), U7.5 (VCC), U14.4 (V+); also elsewhere on the board
/MCU/U_PWM_H: U5.1 (HIN); also elsewhere on the board
/MCU/U_PWM_L: U5.2 (LIN); also elsewhere on the board
/MCU/U_U: U14.1, U14.2 (-); also elsewhere on the board
/MCU/V_PWM_H: U6.1 (HIN); also elsewhere on the board
/MCU/V_PWM_L: U6.2 (LIN); also elsewhere on the board
/MCU/V_U: U14.6 (-), U14.7; also elsewhere on the board
/MCU/W_PWM_H: U7.1 (HIN); also elsewhere on the board
/MCU/W_PWM_L: U7.2 (LIN); also elsewhere on the board
/MCU/W_U: U14.8, U14.9 (-); also elsewhere on the board
/Mosfet driver/U_GH: U5.7 (HO); also elsewhere on the board
/Mosfet driver/U_GL: U5.4 (LO); also elsewhere on the board
/Mosfet driver/U_VP: C45.2, R14.2, U5.6 (VS); also elsewhere on the board
/Mosfet driver/V_GH: U6.7 (HO); also elsewhere on the board
/Mosfet driver/V_GL: U6.4 (LO); also elsewhere on the board
/Mosfet driver/V_VP: C46.2, R49.2, U6.6 (VS); also elsewhere on the board
/Mosfet driver/W_GH: U7.7 (HO); also elsewhere on the board
/Mosfet driver/W_GL: U7.4 (LO); also elsewhere on the board
/Mosfet driver/W_VP: C47.2, R52.2, U7.6 (VS); also elsewhere on the board
GND: C3.2, C42.1, C43.1, C44.1, R15.1, R27.1, R50.1, U5.3 (COM), U6.3 (COM), U7.3 (COM), U14.11 (V-); also elsewhere on the board
unnamed: C45.1, D10.1 (K), U5.8 (VB)
unnamed: C46.1, D11.1 (K), U6.8 (VB)
unnamed: C47.1, D12.1 (K), U7.8 (VB)
unnamed: R12.2, R14.1
unnamed: R28.2, R49.1
unnamed: R51.2, R52.1
unnamed: R12.1, R15.2, U14.3 (+)
unnamed: R27.2, R28.1, U14.5 (+)
unnamed: R50.2, R51.1, U14.10 (+)

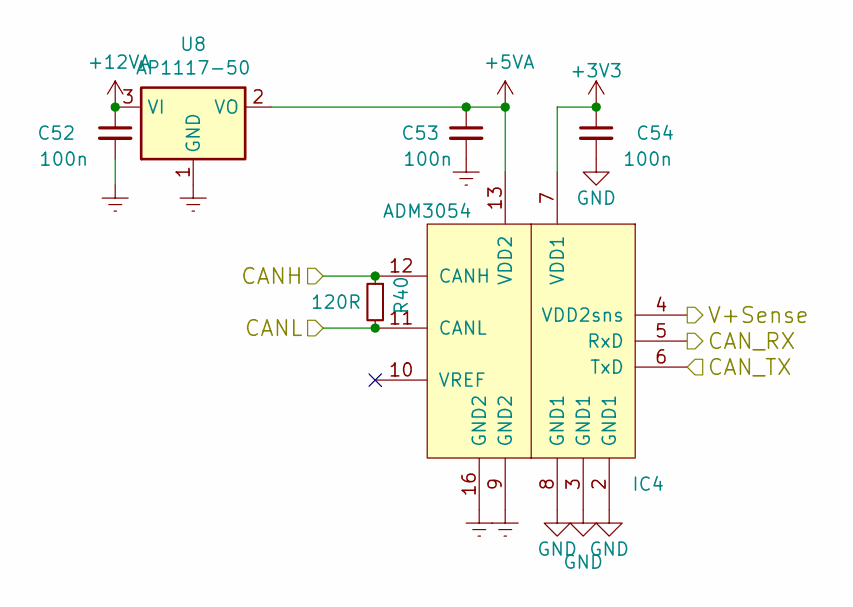
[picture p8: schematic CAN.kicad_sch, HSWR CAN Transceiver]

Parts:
C52, C53, C54: 100n; C_0805_2012Metric
IC4: ADM3054; SOIC-16W_7.5x10.3mm_P1.27mm
R40: 120R; R_0805_2012Metric
U8: AP1117-50; SOT-223-3_TabPin2

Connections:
+3V3: C54.1, IC4.7 (VDD1); also elsewhere on the board
+5VA: C53.1, IC4.13 (VDD2), U8.2 (VO); also elsewhere on the board
+12VA: C52.1, U8.3 (VI); also elsewhere on the board
/CAN bus transceiver/CANH: IC4.12 (CANH), R40.1; also elsewhere on the board
/CAN bus transceiver/CANL: IC4.11 (CANL), R40.2; also elsewhere on the board
/CAN bus transceiver/CAN_RX: IC4.5 (RxD); also elsewhere on the board
/CAN bus transceiver/CAN_TX: IC4.6 (TxD); also elsewhere on the board
/CAN bus transceiver/V+Sense: IC4.4 (VDD2sns); also elsewhere on the board
Earth: C52.2, C53.2, IC4.9 (GND2), IC4.16 (GND2), U8.1 (GND); also elsewhere on the board
GND: C54.2, IC4.2 (GND1), IC4.3 (GND1), IC4.8 (GND1); also elsewhere on the board

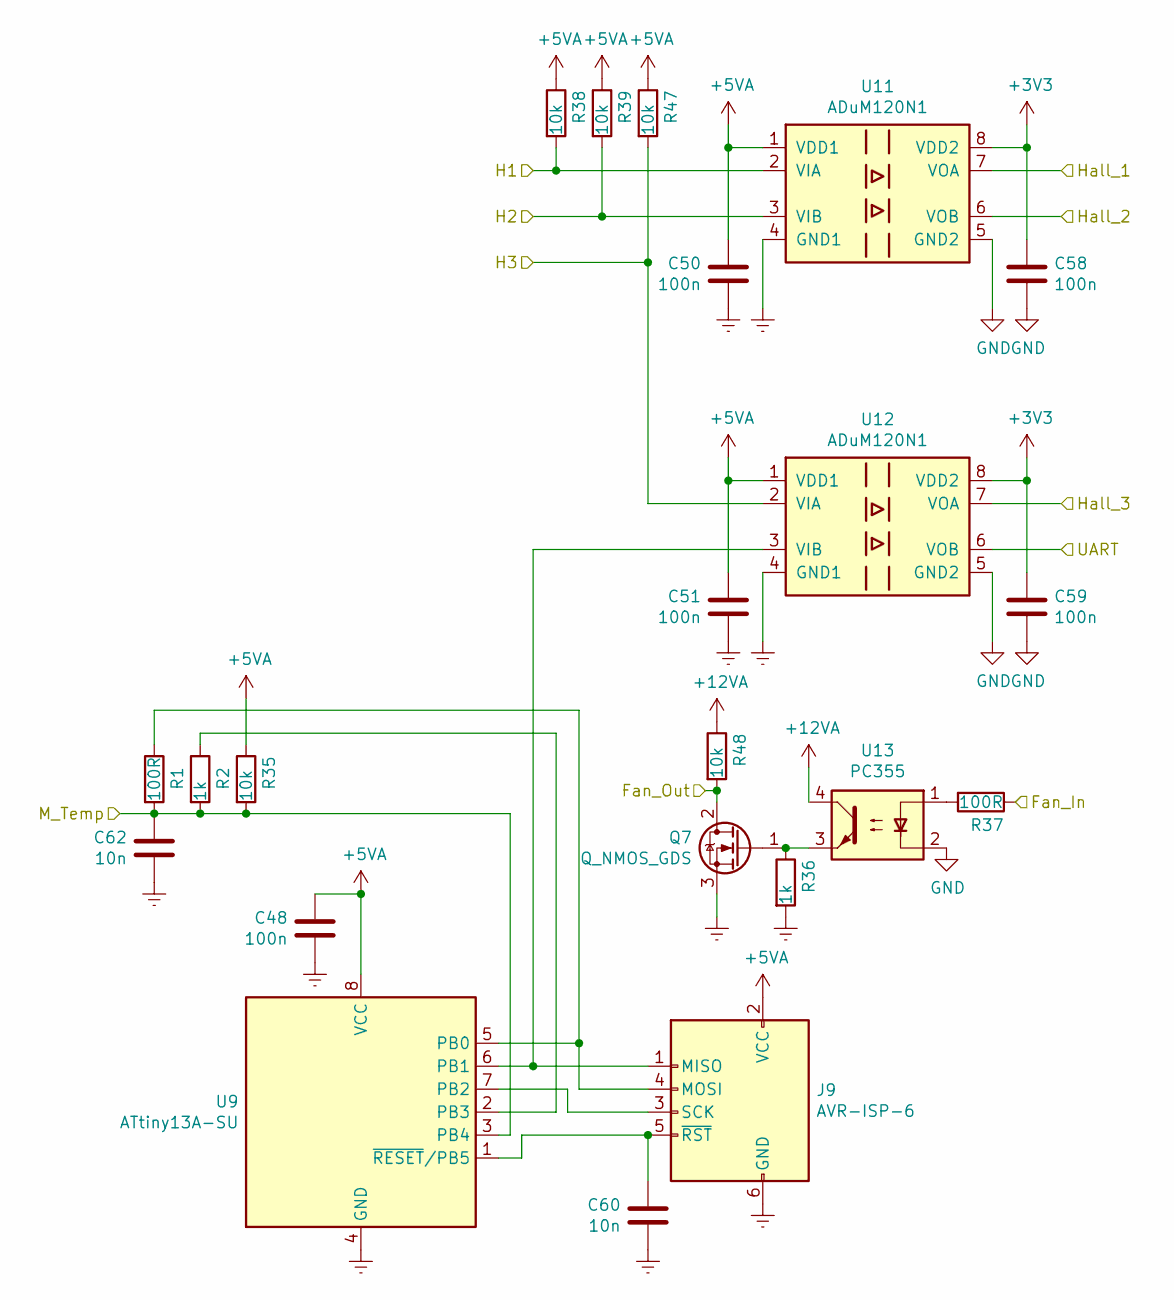
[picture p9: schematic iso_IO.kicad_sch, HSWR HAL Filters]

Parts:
C48, C50, C51, C58, C59: 100n; C_0805_2012Metric
C60, C62: 10n; C_0805_2012Metric
J9: AVR-ISP-6; PinHeader_2x03_P2.54mm_Vertical
Q7: Q_NMOS_GDS; SOT-223-3_TabPin2
R1, R37: 100R; R_0805_2012Metric
R2, R36: 1k; R_0805_2012Metric
R35, R38, R39, R47, R48: 10k; R_0805_2012Metric
U9: ATtiny13A-SU; SOIC-8W_5.3x5.3mm_P1.27mm
U11, U12: ADuM120N1; SOIC-8_3.9x4.9mm_P1.27mm
U13: PC355; SO-4_4.4x4.3mm_P2.54mm

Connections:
+3V3: C58.1, C59.1, U11.8 (VDD2), U12.8 (VDD2); also elsewhere on the board
+5VA: C48.1, C50.1, C51.1, J9.2 (VCC), R35.1, R38.1, R39.1, R47.1, U9.8 (VCC), U11.1 (VDD1), U12.1 (VDD1); also elsewhere on the board
+12VA: R48.1, U13.4; also elsewhere on the board
/MCU/Fan_CPU: R37.1; also elsewhere on the board
/MCU/HALL_1: U11.7 (VOA); also elsewhere on the board
/MCU/HALL_2: U11.6 (VOB); also elsewhere on the board
/MCU/HALL_3: U12.7 (VOA); also elsewhere on the board
/MCU/UART_RX: U12.6 (VOB); also elsewhere on the board
/iso IO/Fan_Out: Q7.2 (D), R48.2; also elsewhere on the board
/iso IO/H1: R38.2, U11.2 (VIA); also elsewhere on the board
/iso IO/H2: R39.2, U11.3 (VIB); also elsewhere on the board
/iso IO/H3: R47.2, U12.2 (VIA); also elsewhere on the board
/iso IO/M_Temp: C62.1, R1.2, R2.2, R35.2, U9.3 (PB4); also elsewhere on the board
Earth: C48.2, C50.2, C51.2, C60.2, C62.2, J9.6 (GND), Q7.3 (S), R36.2, U9.4 (GND), U11.4 (GND1), U12.4 (GND1); also elsewhere on the board
GND: C58.2, C59.2, U11.5 (GND2), U12.5 (GND2), U13.2; also elsewhere on the board
unnamed: J9.1 (MISO), U9.6 (PB1), U12.3 (VIB)
unnamed: J9.4 (MOSI), R1.1, U9.5 (PB0)
unnamed: J9.3 (SCK), U9.7 (PB2)
unnamed: C60.1, J9.5 (~RST), U9.1 (~RESET/PB5)
unnamed: Q7.1 (G), R36.1, U13.3
unnamed: R37.2, U13.1
unnamed: R2.1, U9.2 (PB3)

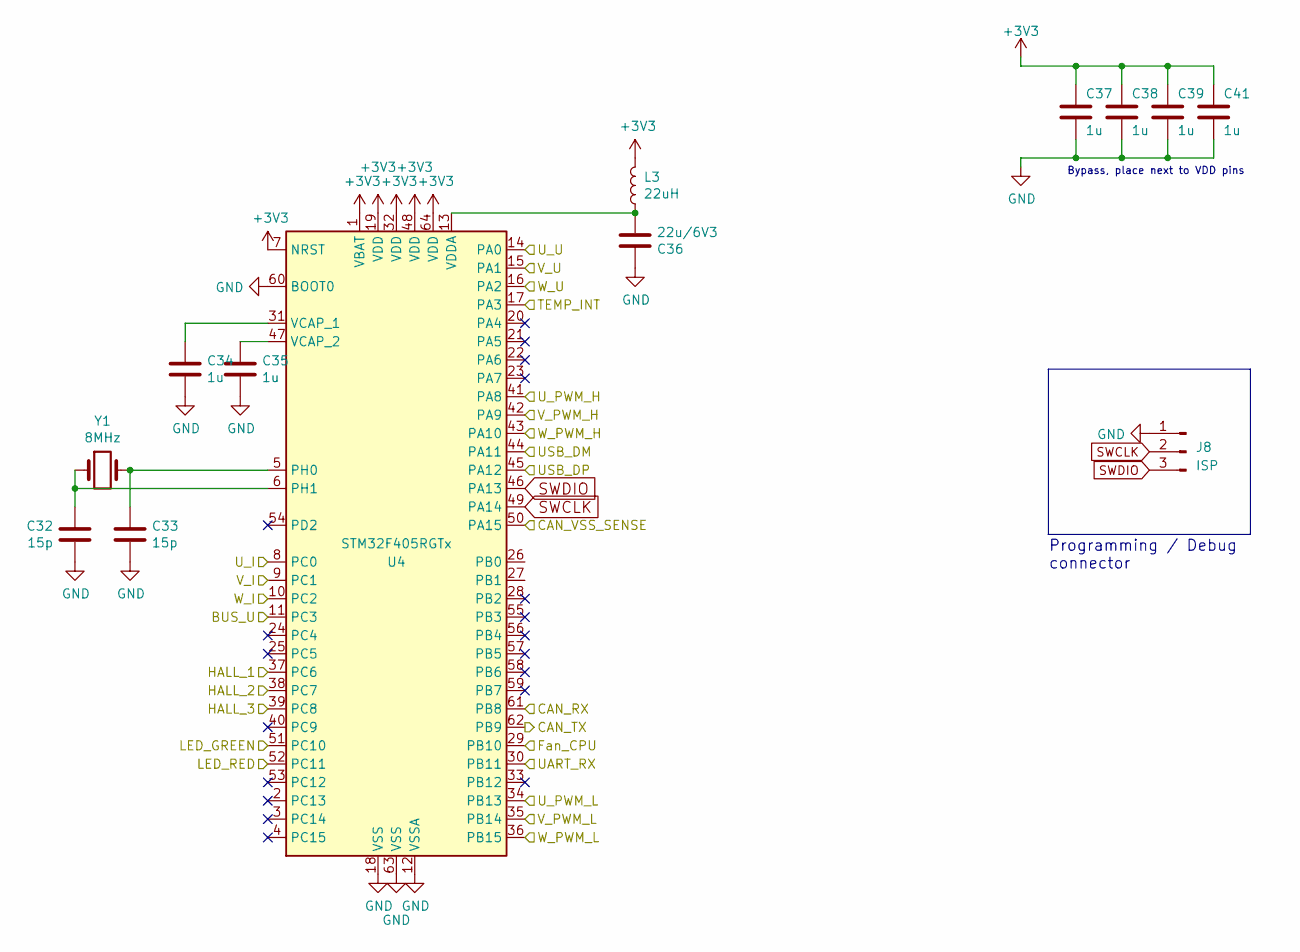
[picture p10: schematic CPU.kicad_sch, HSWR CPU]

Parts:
C32, C33: 15p; C_0805_2012Metric
C34, C35, C37, C38, C39, C41: 1u; C_0805_2012Metric
C36: 22u/6V3; C_0805_2012Metric
J8: ISP; PinHeader_1x03_P2.54mm_Vertical
L3: 22uH; L_0805_2012Metric
U4: STM32F405RGTx; LQFP-64_10x10mm_P0.5mm
Y1: 8MHz; Crystal_HC49-4H_Vertical

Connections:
+3V3: C37.1, C38.1, C39.1, C41.1, L3.2, U4.1 (VBAT), U4.7 (NRST), U4.19 (VDD), U4.32 (VDD), U4.48 (VDD), U4.64 (VDD); also elsewhere on the board
/CAN bus transceiver/CAN_RX: U4.61 (PB8); also elsewhere on the board
/CAN bus transceiver/CAN_TX: U4.62 (PB9); also elsewhere on the board
/CAN bus transceiver/V+Sense: U4.50 (PA15); also elsewhere on the board
/MCU/BUS_U: U4.11 (PC3); also elsewhere on the board
/MCU/Fan_CPU: U4.29 (PB10); also elsewhere on the board
/MCU/HALL_1: U4.37 (PC6); also elsewhere on the board
/MCU/HALL_2: U4.38 (PC7); also elsewhere on the board
/MCU/HALL_3: U4.39 (PC8); also elsewhere on the board
/MCU/LED_GREEN: U4.51 (PC10); also elsewhere on the board
/MCU/LED_RED: U4.52 (PC11); also elsewhere on the board
/MCU/TEMP_INT: U4.17 (PA3); also elsewhere on the board
/MCU/UART_RX: U4.30 (PB11); also elsewhere on the board
/MCU/USB_DM: U4.44 (PA11); also elsewhere on the board
/MCU/USB_DP: U4.45 (PA12); also elsewhere on the board
/MCU/U_I: U4.8 (PC0); also elsewhere on the board
/MCU/U_PWM_H: U4.41 (PA8); also elsewhere on the board
/MCU/U_PWM_L: U4.34 (PB13); also elsewhere on the board
/MCU/U_U: U4.14 (PA0); also elsewhere on the board
/MCU/V_I: U4.9 (PC1); also elsewhere on the board
/MCU/V_PWM_H: U4.42 (PA9); also elsewhere on the board
/MCU/V_PWM_L: U4.35 (PB14); also elsewhere on the board
/MCU/V_U: U4.15 (PA1); also elsewhere on the board
/MCU/W_I: U4.10 (PC2); also elsewhere on the board
/MCU/W_PWM_H: U4.43 (PA10); also elsewhere on the board
/MCU/W_PWM_L: U4.36 (PB15); also elsewhere on the board
/MCU/W_U: U4.16 (PA2); also elsewhere on the board
GND: C32.1, C33.2, C34.2, C35.2, C36.1, C37.2, C38.2, C39.2, C41.2, J8.1, U4.12 (VSSA), U4.18 (VSS), U4.60 (BOOT0), U4.63 (VSS); also elsewhere on the board
unnamed: C33.1, U4.5 (PH0), Y1.2
unnamed: C32.2, U4.6 (PH1), Y1.1
unnamed: C34.1, U4.31 (VCAP_1)
unnamed: C35.1, U4.47 (VCAP_2)
unnamed: C36.2, L3.1, U4.13 (VDDA)
SWCLK: J8.2, U4.49 (PA14)
SWDIO: J8.3, U4.46 (PA13)

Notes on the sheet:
Bypass, place next to VDD pins
Programming / Debug connector

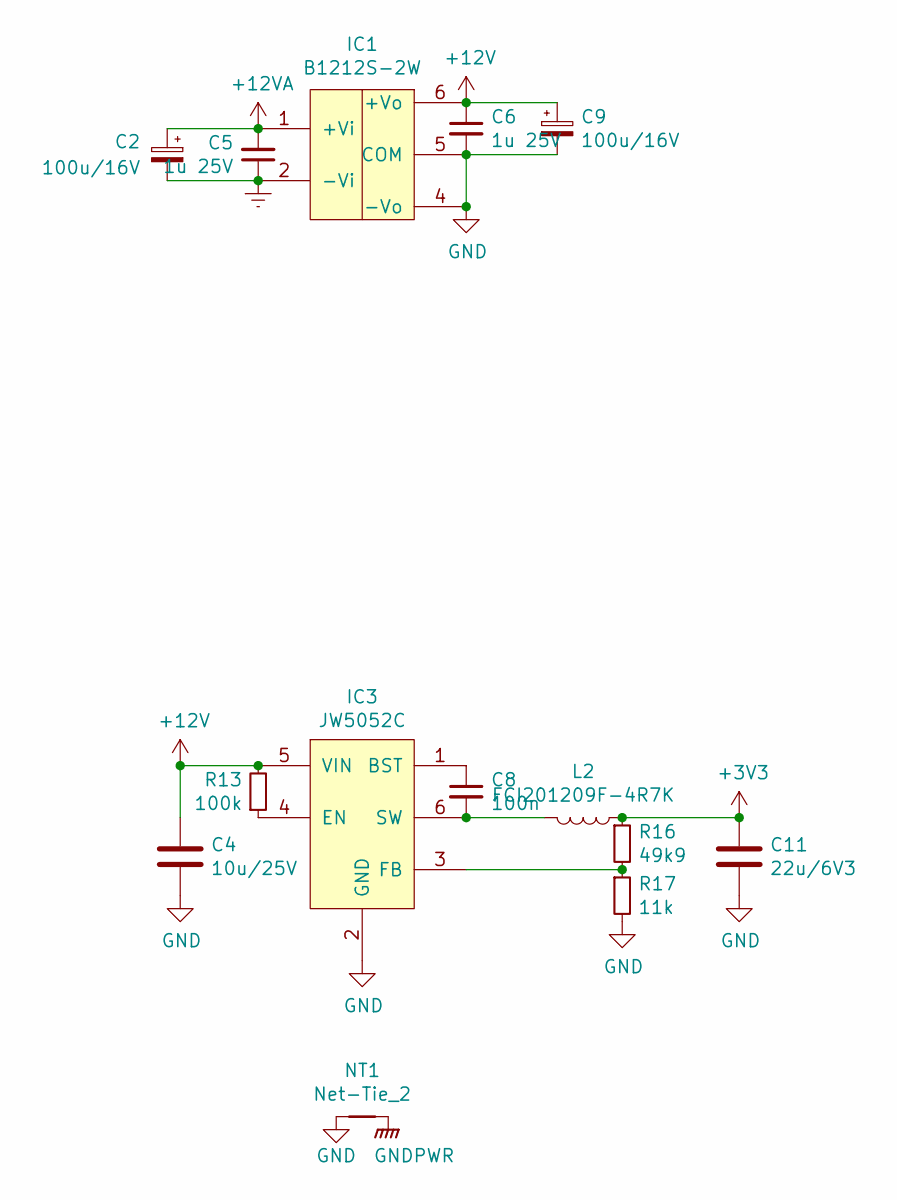
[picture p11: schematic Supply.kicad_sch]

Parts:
C2, C9: 100u/16V; CP_Radial_D6.3mm_P2.50mm
C4: 10u/25V; C_0805_2012Metric
C5, C6: 1u 25V; C_0805_2012Metric
C8: 100n; C_0805_2012Metric
C11: 22u/6V3; C_0805_2012Metric
IC1: B1212S-2W; Converter_DCDC_muRata_NMAxxxxSC_THT
IC3: JW5052C; TSOT-23-6
L2: FCI201209F-4R7K; L_0805_2012Metric
NT1: Net-Tie_2; NetTie-2_SMD_Pad2.0mm
R13: 100k; R_0805_2012Metric
R16: 49k9; R_0805_2012Metric
R17: 11k; R_0805_2012Metric

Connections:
+3V3: C11.1, L2.1, R16.1; also elsewhere on the board
+12V: C4.1, C6.1, C9.1, IC1.6 (+Vo), IC3.5 (VIN), R13.2; also elsewhere on the board
+12VA: C2.1, C5.2, IC1.1 (+Vi); also elsewhere on the board
Earth: C2.2, C5.1, IC1.2 (-Vi); also elsewhere on the board
GND: C4.2, C6.2, C9.2, C11.2, IC1.4 (-Vo), IC1.5 (COM), IC3.2 (GND), NT1.1, R17.2; also elsewhere on the board
GNDPWR: NT1.2; also elsewhere on the board
unnamed: C8.1, IC3.1 (BST)
unnamed: IC3.4 (EN), R13.1
unnamed: IC3.3 (FB), R16.2, R17.1
unnamed: C8.2, IC3.6 (SW), L2.2

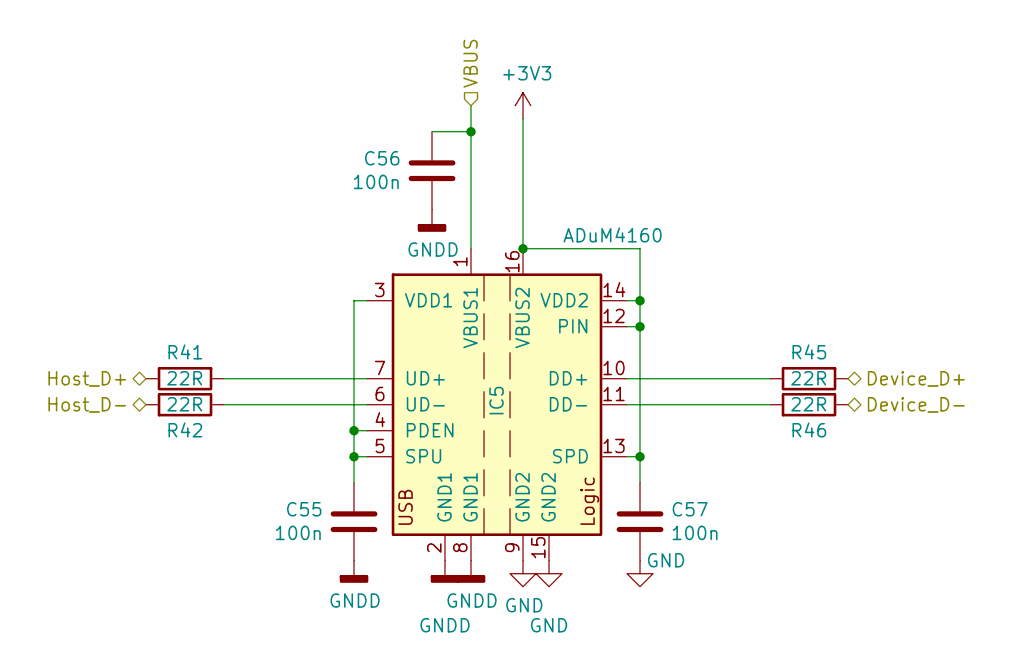
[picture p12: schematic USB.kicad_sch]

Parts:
C55, C56, C57: 100n; C_0805_2012Metric
IC5: ADuM4160; SOIC-16W_7.5x10.3mm_P1.27mm
R41, R42, R45, R46: 22R; R_0805_2012Metric

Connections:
+3V3: C57.2, IC5.12 (PIN), IC5.13 (SPD), IC5.14 (VDD2), IC5.16 (VBUS2); also elsewhere on the board
/MCU/USB_DM: R46.1; also elsewhere on the board
/MCU/USB_DP: R45.2; also elsewhere on the board
/USB/Host_D+: R41.1; also elsewhere on the board
/USB/Host_D-: R42.2; also elsewhere on the board
/USB/VBUS: C56.2, IC5.1 (VBUS1); also elsewhere on the board
GND: C57.1, IC5.9 (GND2), IC5.15 (GND2); also elsewhere on the board
GNDD: C55.1, C56.1, IC5.2 (GND1), IC5.8 (GND1); also elsewhere on the board
unnamed: IC5.10 (DD+), R45.1
unnamed: IC5.11 (DD-), R46.2
unnamed: C55.2, IC5.3 (VDD1), IC5.4 (PDEN), IC5.5 (SPU)
unnamed: IC5.7 (UD+), R41.2
unnamed: IC5.6 (UD-), R42.1

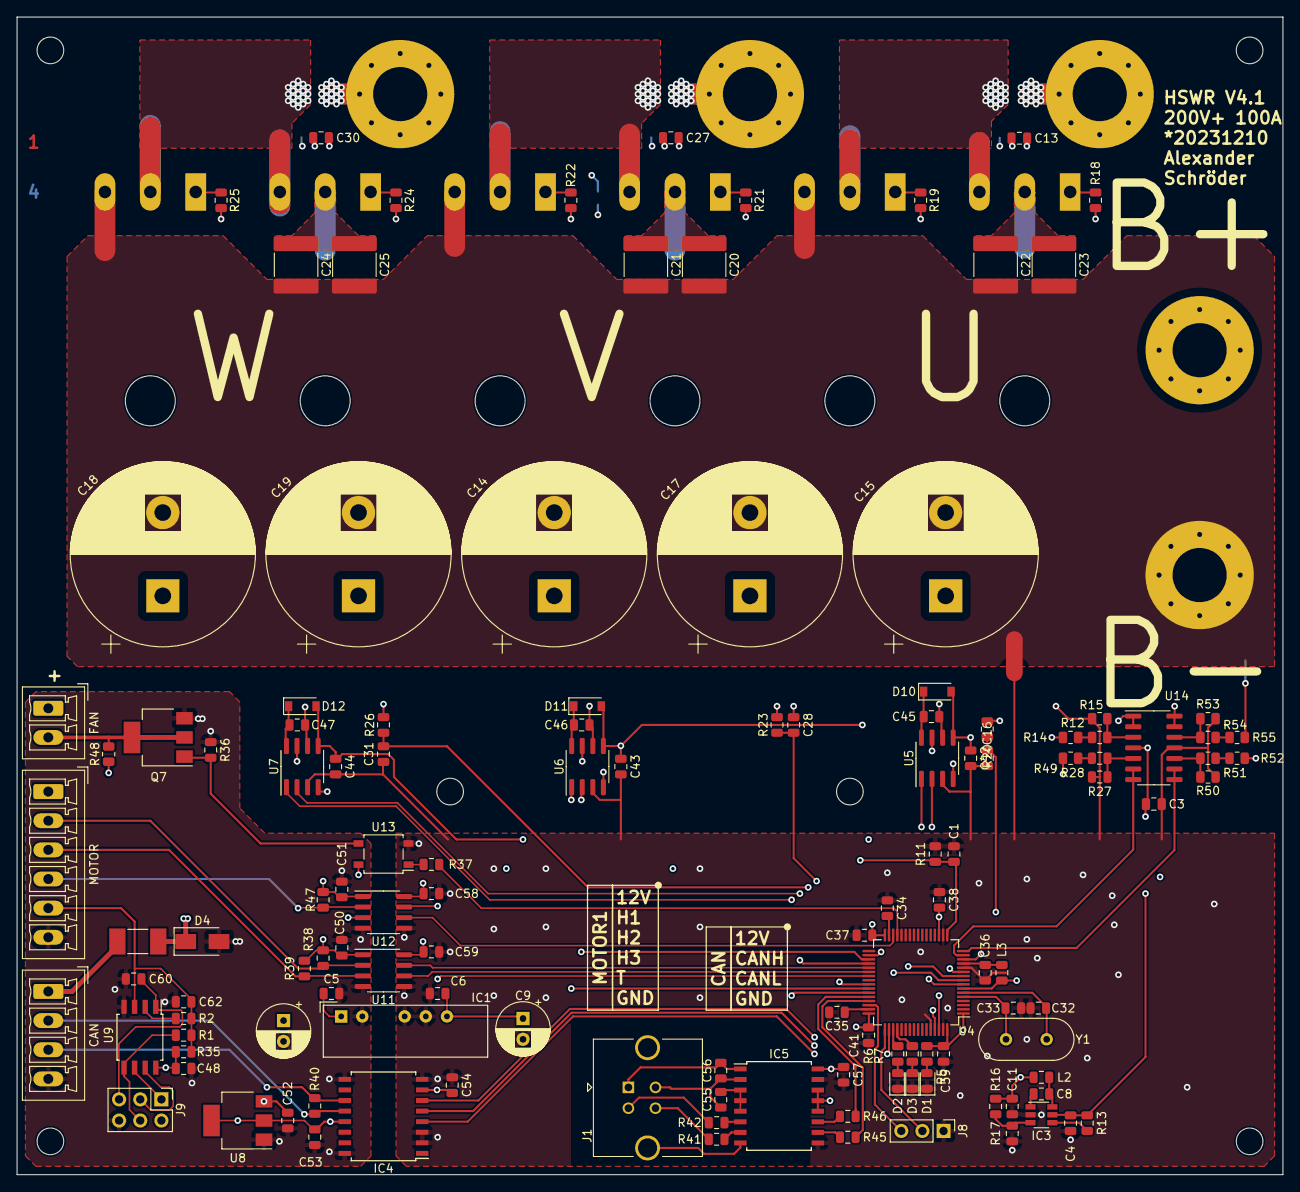
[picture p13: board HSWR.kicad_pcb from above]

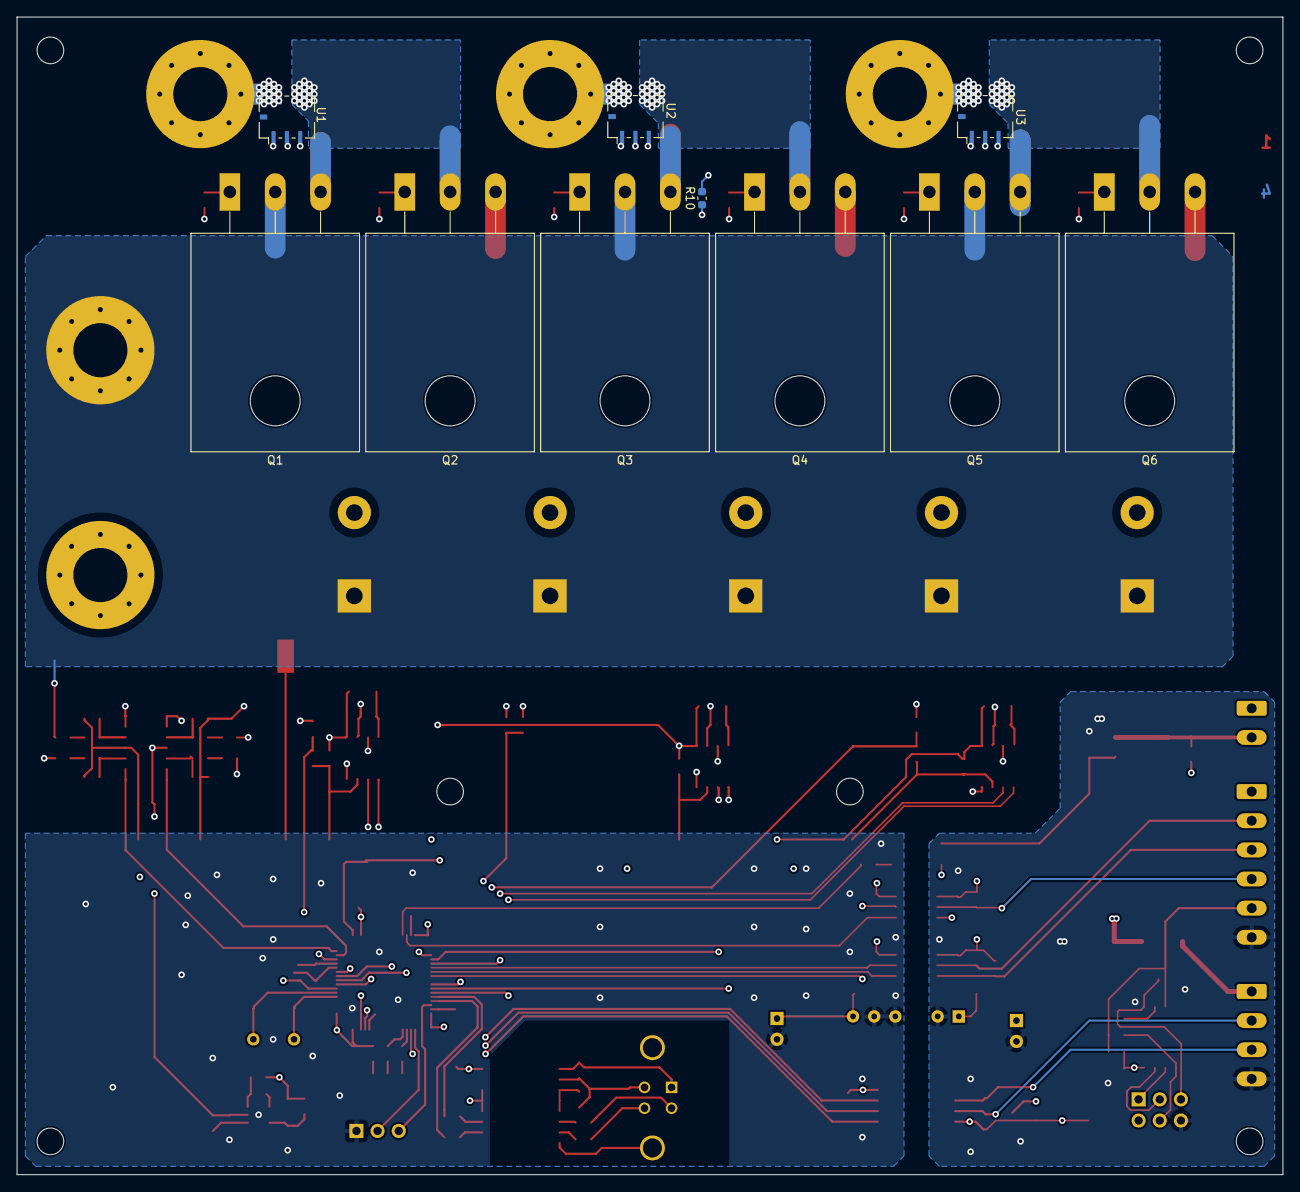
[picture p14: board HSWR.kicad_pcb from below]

Board: 4 copper layers, 152.0 x 139.0 mm, 144 parts (10 on the bottom side), 104 nets.

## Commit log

2017-03-26 - V2.0 productiion run
    [CAN.sch, CPU.sch, HSWR V2.kicad_pcb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]
2017-03-26 Added discription and link to forum thread
2017-04-28 ~ changed gate resistance to 1R ~ changed power mosfet to IRFP4668PBF
    [CAN.sch, CPU.sch, HSWR V2.sch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]
2017-06-23 - 100A in 50A geändert
    [CPU.sch, HSWR V2.sch]
2017-07-30 ~ removed/optionalised INA240 input filter ~ raised load resisitance of sense resistors for lower power loss ~ adopted old division factor on phase voltage sense deviders
    [CPU.sch, HSWR V2.kicad_pcb, HSWR V2.sch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]
2018-08-05 - changed dividers to 220k vs 3k3 - changed hall supply to +5V instead of +3V3
    [CAN.sch, CPU.sch, HSWR V2.kicad_pcb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]
2018-08-06 - updated project to 5.0.0 - added ignore file
    [CAN.sch, CPU.sch, HSWR V2.kicad_pcb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]
2019-03-27 - updated to VESC6 architecture - still some things to do in schematic
    [CAN.sch, CPU.sch, HSWR V2.kicad_pcb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]
2019-03-27 - started layout - high current path finished - some work on gate drivers
    [HSWR V2.kicad_pcb, Power.sch, mosfets.sch]
2019-03-27 - gate drivers routed - CSAs routed - HV/PA nets routed
    [HSWR V2.kicad_pcb, HSWR V2.sch, Power.sch]
2019-03-28 - layout pretty much finished except PSU and maaaaybe R2D - started work on R2D with AD2S1205
    [CAN.sch, CPU.sch, HSWR V2.kicad_pcb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]
2019-03-29 - removed R2D.sch - selected PSUs - finished layout
    [CAN.sch, CPU.sch, HSWR V2.kicad_pcb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]
2019-03-29 - optimized high current polygon
    [HSWR V2.kicad_pcb]
2019-04-02 - corrected current filter resistors - adapted USB footprint - added 0.1% note to dc bus voltage divider
    [CAN.sch, HSWR V2.kicad_pcb, HSWR V2.sch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]
2020-01-17 - rescued schematic - added *.sch-bak to ignore - fixed bypass diode polarity - fixed PDEN being low - added 0R resistors instead of USB iso option - added caps to DCDC - added filter to VDDA
    [CAN.sch, CPU.sch, HSWR V2.kicad_pcb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]
2020-02-13 - changed CSA for Hall effect sensors - updated power stage layout
    [CAN.sch, CPU.sch, HSWR V2.kicad_pcb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]
2020-02-13 - removed rescue lib and symbols - added HSWR.lib
    [CAN.sch, CPU.sch, HSWR V2.kicad_pcb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]
2020-02-29 - reworked IO section -> now fully isolated - added fan output - sensor IO is now differential - exposed differential UART interface - fan pin not defined yet!
    [CAN.sch, CPU.sch, HSWR.kicad_pcb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]
2020-03-02 - added high power capabilities to fan output - moved CAN isolator - connected fan output to PB10 (TIM2_CH3)
    [CAN.sch, CPU.sch, HSWR.kicad_pcb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]
2020-03-04 - optimized silk screen - fixed some final missing traces
    [HSWR.kicad_pcb]
2020-03-05 - fixed ISP connector being mirrored - changed some footprints to get them 3D Models - added a preliminary BOM
    [BOM.xlsx, CPU.sch, HSWR.kicad_pcb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]
2020-03-05 - removed some unused symbols from HSWR.lib - changed U8 (linear reg) to standard symbol - fixed wrong footprint for C24
    [CAN.sch, HSWR.kicad_pcb, mosfets.sch]
2020-03-05 - enlarged isolated island - bigger package for fan MOSFET - added 12V input protection - added U_DC sensing filter - added M_temp input filter - added reset pin decoupling for AVR - added HALL pull-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
    [CAN.sch, CPU.sch, HSWR.kicad_pcb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]
2020-05-22 - specialized TO264 package for bigger screw hole
    [CAN.sch, CPU.sch, HSWR.kicad_pcb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]
2020-05-26 - reworked silkscreen
    [HSWR.kicad_pcb]
2020-05-26 - renamed ADUM3054 as ADM3054 - specified ADuM120N1 (fail high)
    [CAN.sch, HSWR.kicad_pcb, iso_IO.sch]
2020-07-09 - added fiducials - updated silkscreen - removed ghost traces - optimized top layer polygons - increased insulation distance on HV nets - added vias around current sensor to make use of inner layers
    [HSWR.kicad_pcb]
2020-07-13 - last finishing touches - export check - updated README.md
    [HSWR.kicad_pcb]
2020-10-06 - updated schematic symbols - updated silk screen version label
    [HSWR.kicad_pcb, Supply.sch, iso_IO.sch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]
2020-10-06 - removed 5V DCDC because unused
    [HSWR.kicad_pcb, Supply.sch]
2020-10-22 - updated schematic textbox (version, author)
    [CAN.sch, CPU.sch, HSWR.sch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]
2021-06-08 - changed gate resistors to 4R7
    [mosfets.sch]
2021-07-08 - added missing 3D models to layout
    [CP_Radial_D220mm_P1000mm_3pin_SnapIn.step, HSWR.kicad_pcb, TO-264-3-HM.step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]
2023-07-11 - upgraded project to KiCAD 7 - cleaned project - changed hall pullups to 10k
    [CAN.kicad_sch, CAN.sch, CPU.kicad_sch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]
2023-11-16 HSWR V4.1: - added opamp for better voltage measurement
    [CPU.kicad_sch, HSWR.kicad_pcb, HSWR.kicad_sch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]
2023-12-08 - peeled back the filler planes around HV logic - improved insulation on HV logic
    [CPU.kicad_sch, HSWR.kicad_pcb, HSWR.kicad_sch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]
2023-12-10 - added pinouts to connectors - last fixes before export
    [HSWR.kicad_pcb]
2024-03-19 - fixed some bugs
    [CPU.kicad_sch, HSWR.kicad_pcb]
2024-11-06 - upgraded to KiCAD8
    [CAN.kicad_sch, CPU.kicad_sch, HSWR.kicad_sch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]
